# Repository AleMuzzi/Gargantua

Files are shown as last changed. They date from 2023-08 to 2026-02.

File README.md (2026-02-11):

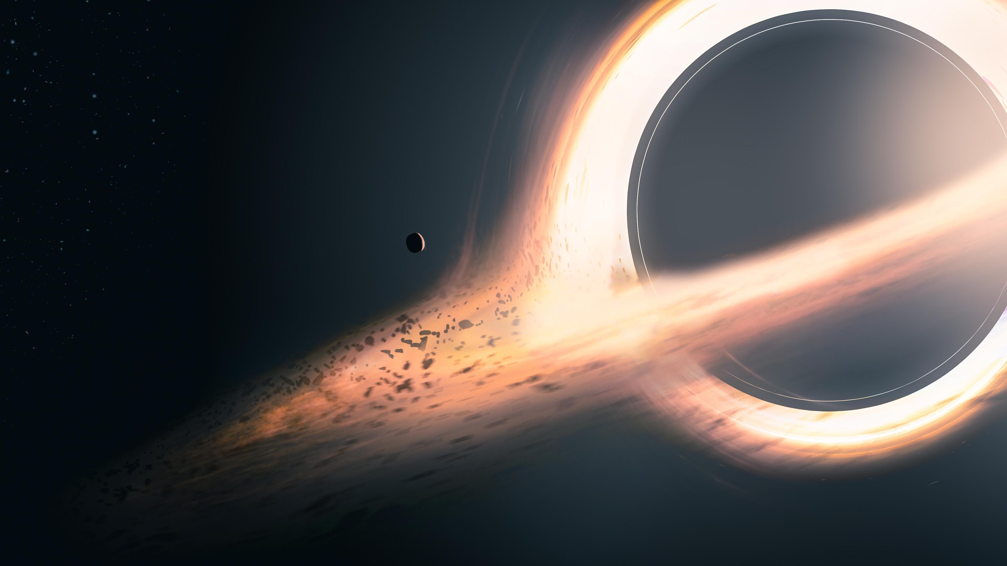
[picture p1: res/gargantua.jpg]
Gargantua Black Hole

# Gargantua - Large Format 3D Printer

With the prominence of the famous supermassive black hole, this is Gargantua!

Gargantua has a giant **430x420x770mm build volume** with double extruder and double independent Z axis to improve stability. Running **Klipper**, it enables for remote control from any device.

<p align="center">
  BTT Manta M8P
</p>

### Technical Specifications
```
Build Volume:           400x400x768 mm                   
Dimesions:                                        Extruders number:              2                   
    printer:            620x625x1145mm            Max extruders temperature:  300°      
    with case:         1020x890x1350mm            Max bed temperature:        110°         
    + dehumidifier:    1020x890x1790mm            Enclosure:                    Sì                          
Precision:                      0.1 mm            OS:                      Klipper                              
Max speed:                    300 mm/s            Power:               2x 24V 500W               
```
---

### Hardware

Choosing the firmware was the first major decision, as it influenced all subsequent hardware choices.
**Klipper** emerged as the winner due to its flexibility and ability to leverage 32-bit hardware for precise movement and temperature control.
I already had experience with Marlin, but I wanted to explore new possibilities and Klipper seemed like the right choice for this project.

<table align="right">
  <tr>
    <td align="center">
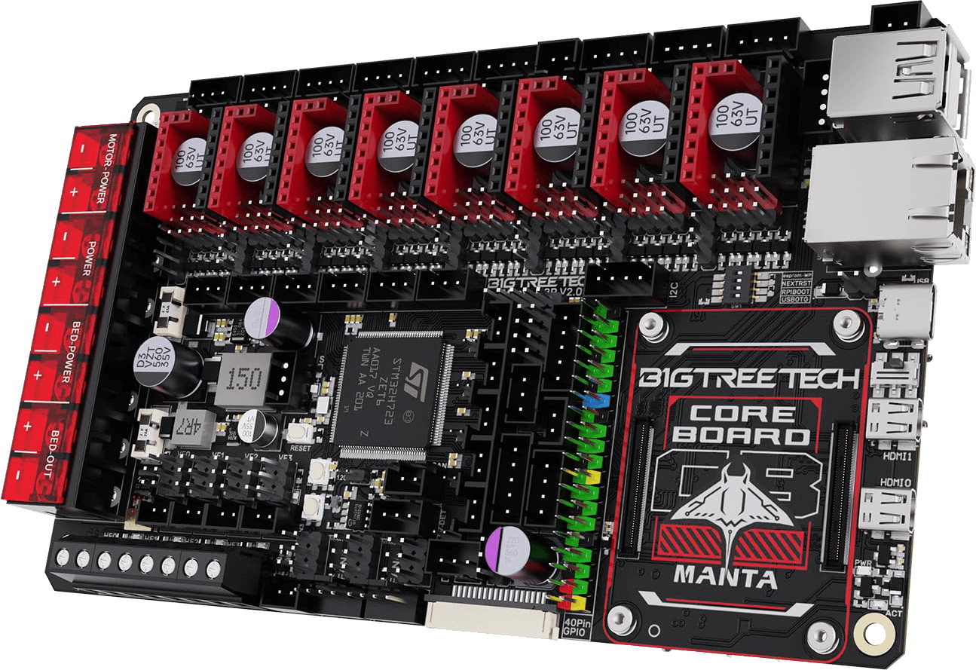
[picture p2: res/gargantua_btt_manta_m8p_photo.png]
BTT Manta M8P
      <br/>
      <sub><i>BTT Manta M8P</i></sub>
    </td>
  </tr>
</table>

For the controller I chose the **BTT Manta M8P** board, a 32-bit control board based on the STM32G0B1VET6, a 32-bit 64MHz ARM Cortex-M0+, which offers a wide range of features and good compatibility with various open source firmware.
It is paired with the **BTT CB1** computing module (essentially a twin to the Raspberry Pi CM4), which runs Klipper and manages the **Mainsail**[<math display="inline"><sup>↗</sup></math>](https://github.com/mainsail-crew/mainsail) user interface.

The next step was selecting the stepper motors. To reuse as many components as possible from my Ender 3 Pro, I decided to keep the same **NEMA 17** motors, which have proven reliable and suitable for the needs of this project, pairing them with a dual-axis **CR 42-60** motor for the Y-axis, drawing inspiration from the Creality CR-6 Max setup.

Also from the Creality CR-6 Max I took the heated bed, which offers a large printing surface of **400x400mm** and uniform heat distribution, and the idea of adding a couple of diagonal tie rods to improve the stability of the structure.

The motors are driven by **TMC2209** drivers, known for their silent operation and advanced microstepping.

<table align="right">
  <tr>
    <td align="center">
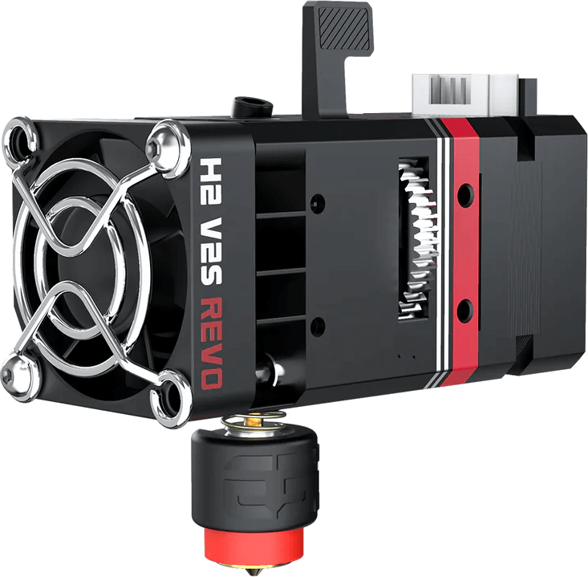
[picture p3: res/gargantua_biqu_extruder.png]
Biqu H2 V2S REVO
      <br/>
      <sub><i>Biqu H2 V2S REVO</i></sub>
    </td>
  </tr>
</table>

Because of the high power draw of the massive bed and dual hotends, I calculated the following power requirements:

The total power required by the main components of the printer is as follows:
- **Heated Bed:** 420W @ 24V
- **2x Biqu H2 V2S REVO Hotends (up to 300°):** 40W each
- **Filament Drying System (ongoing project):** 200W
- **Other components**: motors, fans, electronics
- **Safety margin**

So, I opted for **two 24V 500W power supplies**—one dedicated solely to the bed and the other for all other components. The bed is controlled via a **Solid State Relay (SSR)** for safety and reliability.

Finally, I upgraded the bed leveling sensor from a standard probe to a **Beacon H**[<math display="inline"><sup>↗</sup></math>](https://beacon3d.com/), which uses eddy current displacement to measure distance to accurately measure the distance between the sensor and the print bed, offering much more accurate, reliable and faster calibration, especially on larger surfaces. This allowed the bed mesh to leap from a 5x5 grid to a highly accurate 30x30 matrix without needing interpolation.

<p align="center">
  <video src="https://github.com/user-attachments/assets/059d04e4-c965-48ba-bb5d-aec4066f602b" width="40%" controls loop muted autoplay playsinline/>
</p>
<p align="center">
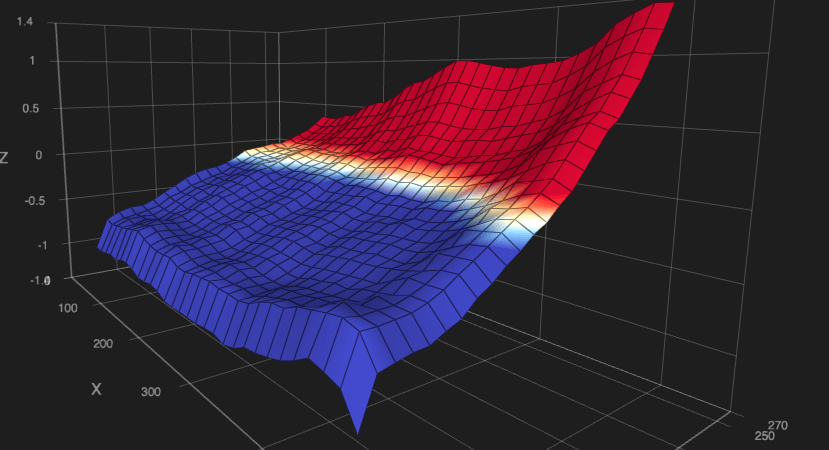
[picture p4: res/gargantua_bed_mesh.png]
Gargantua bed mesh
  
</p>

<p align="center">
  <sub><i>The plate seems very tilted, but if you look carefully at the Z-axis, on 40cm of length there is only 2mm of maximum difference</i></sub>
</p>

### Design and Development

The printer design was done using **Fusion 360**, which allowed me to precisely design each component, simulate axis movement, and verify the integration of all hardware components. I created detailed 3D models for every part of the printer, including motor mounts, heated dish brackets, electronics mounts, and cooling components.
The development process was iterative, with frequent testing and design changes. Designing everything in CAD allowed me to identify and resolve potential compatibility and space issues before proceeding to the assembly phase, saving time and resources.
The project was initially manageable in size, but over time it was necessary to break it down into parts and combine them into a single design for when an overall view is needed. This modularity allowed for more agile development of the various components.

<p align="center">
  Gargantua printer structure<br/>
  <sub><i>Gargantua's structure</i></sub>
</p>

#### From Bowden to Direct Drive

The Creality Ender 3 Pro uses a "bowden" extrusion system, in which the extruder is separated from the hotend and the filament is pushed through a tube to the hotend.
This approach has some advantages, such as reducing weight on the X-axis, but can present problems of reactivity and precision in extrusion, especially with flexible materials. I had already had difficulty with this system when trying to print TPU, which tended to bend inside the bowden tube, so I decided to switch to a "direct drive" system, where the extruder is mounted directly on the hotend. This change significantly improved the precision and responsiveness of the extrusion, allowing me to print a wider range of materials with greater reliability.
In designing this printer, flexibility took priority over performance; if I were to start over with a CoreXY system, I would probably opt for a bowden extrusion system, to reduce the weight on the X-axis and improve printing speed, at the cost of not being able to print flexible materials.

#### Dual Extruder

The idea of being able to print with two extruders has always fascinated me: in addition to allowing printing in 2 colors, it allows you to experiment with different materials, such as prints in which a flexible and a non-flexible material are interleaved, or to use soluble media such as PVA.
I then decided to implement it from the beginning, designing a support head for two Biqu H2 V2S REVO hotends.

<p align="center">
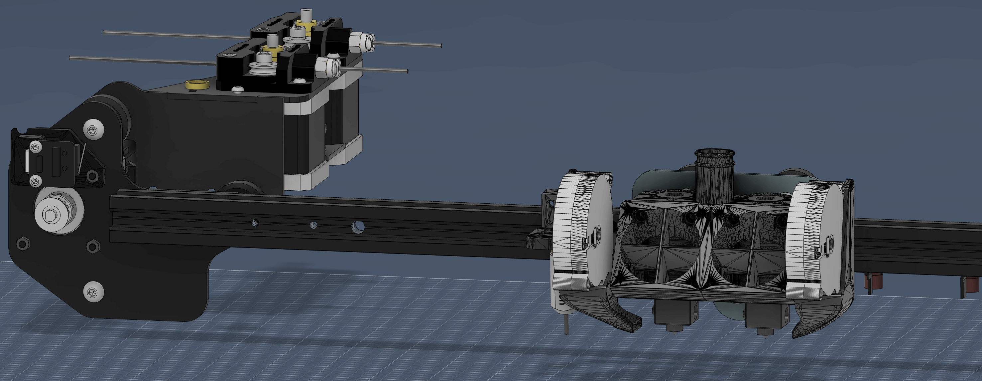
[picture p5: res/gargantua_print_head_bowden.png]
Gargantua bowden print head
  <br/>
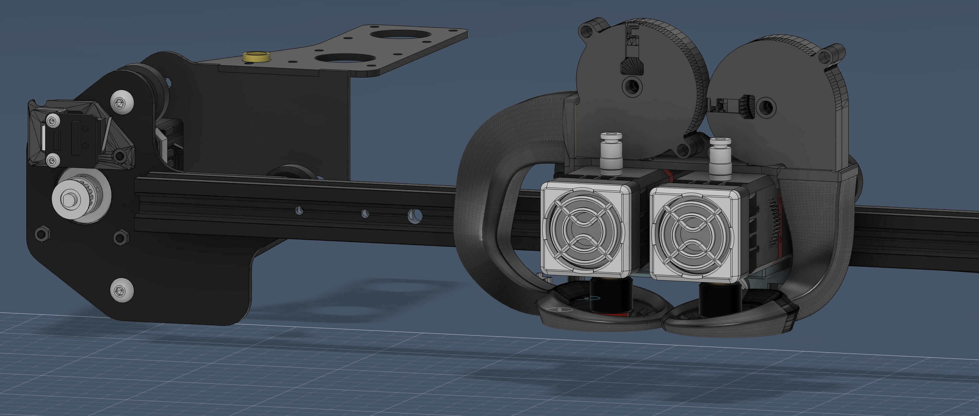
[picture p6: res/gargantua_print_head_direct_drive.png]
Gargantua direct drive print head
  <br/>
  <sub><i>(above) Bowden extruder, (below) Direct drive extruder</i></sub>
</p>

In the images above you can see the difference between the print head with bowden extruders and the one with direct drive extruders.
In the first, you can glimpse the extruders and the aeration channels to cool them (hidden fans to show the details), and in the distance on the left, the extruder motors.
In the second, however, you can see the two extruder motors mounted directly on the hotends on the print head. The metal profile where the motors for the bowden system were housed was left mounted to have an anchor for the cables going to the head.

In addition to the extruders, it can be noted that the aeration channels of the workpiece, fed by two radial fans, have also been improved, to allow for more homogeneous cooling.

#### Enclosure
To improve print quality, reduce noise during printing, and issues related to warping parts when printing materials like ABS, I decided to build a printer enclosure, a structure that completely encloses the printer, maintaining a stable internal temperature and reducing the influence of external air currents.
I already had experience building enclosures, for my Ender 3 Pro I had built what on the internet is called "IKEA Lack Enclosure"[<math display="inline"><sup>↗</sup></math>](https://www.google.com/search?q=ikea+lack+enclosure): using two overlapping IKEA Lack coffee tables, plexiglass panels for the side walls and doors, and 3D printing the various connectors.
As a first enclosure it might have been fine, but the IKEA Lack coffee table did not provide the necessary stability, and in any case it would not have been a solution applicable to a large printer like Gargantua.

For Gargantua, I drew a hollow aluminum square-section profile structure, with two ports, so that I had both front and side access to the printer.

<p align="center">
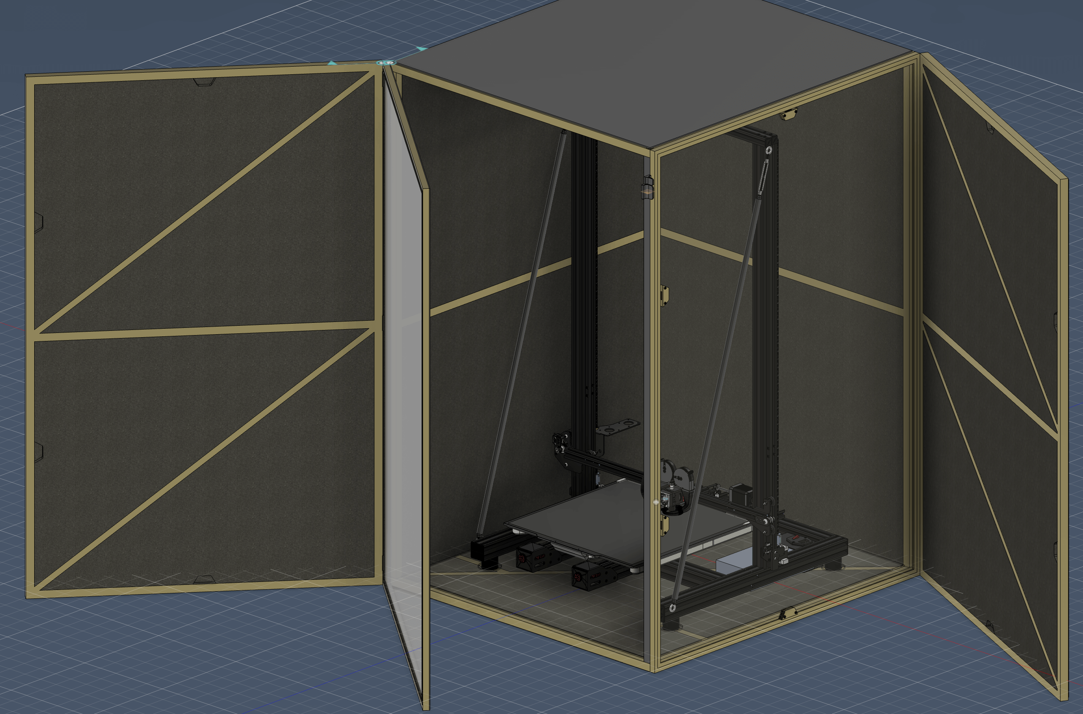
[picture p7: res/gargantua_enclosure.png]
Gargantua enclosure
  <br/>
  <sub><i>Gargantua inside its enclosure</i></sub>
</p>

The walls and doors were then padded with insulation panels and covered with hard plastic panels.
To allow me to inspect the printing in progress without having to open the doors, I designed the doors with a double hinge, so that the outer part can be opened independently of the inner part, consisting of an aluminum frame with a transparent plexiglass panel.
Inside, the printer is attached to the enclosure through 4 rubber dampers, to reduce vibrations transmitted to the structure, which is also equipped with rubber dampers such as feet.

> ℹ️ The enclosure is necessarily non-square in base to minimize the size while leaving room for the plate to slide along the Y-axis.

A strip led system was installed on the ceiling of the enclosure, to illuminate the interior during printing and facilitate visual inspection of the printing process.

<p align="center">
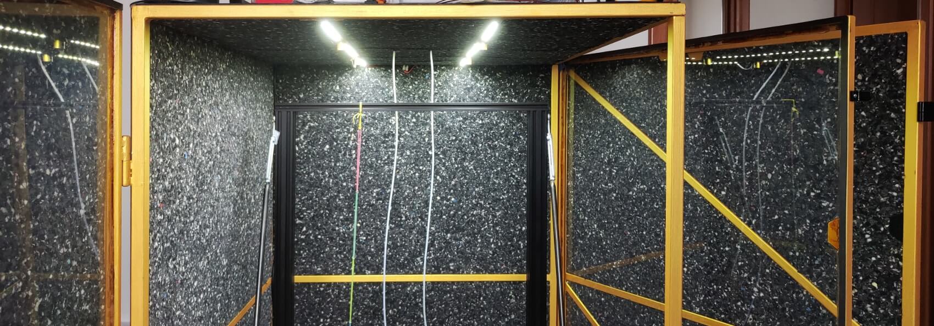
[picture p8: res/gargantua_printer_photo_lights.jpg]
Gargantua lights
  
</p>

### Filament Dehumidifier

A crucial and often underestimated part of 3D printing is the management of filaments, which are hygroscopic and tend to absorb moisture from the environment, resulting in a degradation of print quality. A wet filament expands and can cause under-extrusion problems, or even extruder blockages.
To address this issue, I decided to integrate a filament drying system directly above the enclosure, designing a dedicated compartment that houses 10 filaments, with a heating and ventilation system to keep the filaments dry and ready for printing.
This system is powered together with the printer, and is connected directly to the extruders, so that the dried filaments do not come into contact with external moisture on the way to the hotends.

<p align="center">
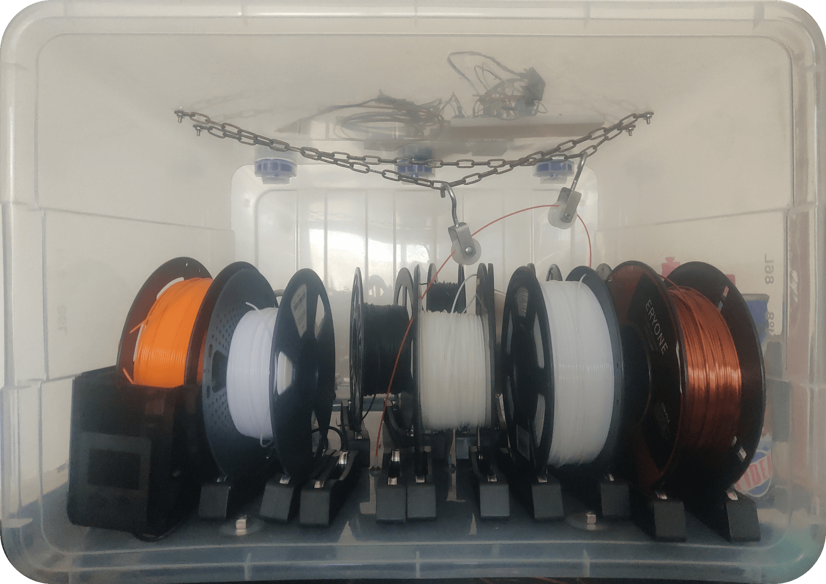
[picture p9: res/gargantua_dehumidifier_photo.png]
Gargantua dehumidifier
  <br/>
  <sub><i>Filament dehumidifier</i></sub>
</p>

In the photo above, you can see the dehumidifier, with several filaments, and above it, you can see the heating circuit, still in the prototyping phase. In the center, a pulley system guides the filaments toward the extruders; at the bottom center, you can see the tube that carries the filaments out of the dehumidifier, toward the extruders.

The system is still in development; the circuit is ready and tested, but some modifications to the 3D design are still needed to better integrate the components and improve airflow.

### Fume Management

Printing with materials such as ABS can generate potentially harmful fumes, as well as an unpleasant odor. To improve safety and comfort during printing, I decided to integrate a smoke extraction system directly into the enclosure.
Since I didn't have access to an external exhaust, I opted for an air filtration system based on activated carbon and HEPA filters, which capture particles and neutralize odors before reintroducing air into the environment.
The filter in question is the **AlveoOne R of Alveo3D**[<math display="inline"><sup>↗</sup></math>](https://www.alveo3d.com/en/product/alveoone-r-assembled/), designed specifically for 3D printing, it filters the air present in the enclosed case.
Gargantua's firmware is configured to automatically activate the fume extraction system when fume-generating materials are printed, and to continue filtering the air for a certain period after printing has finished.

### The Name: Gargantua
<p align="center">
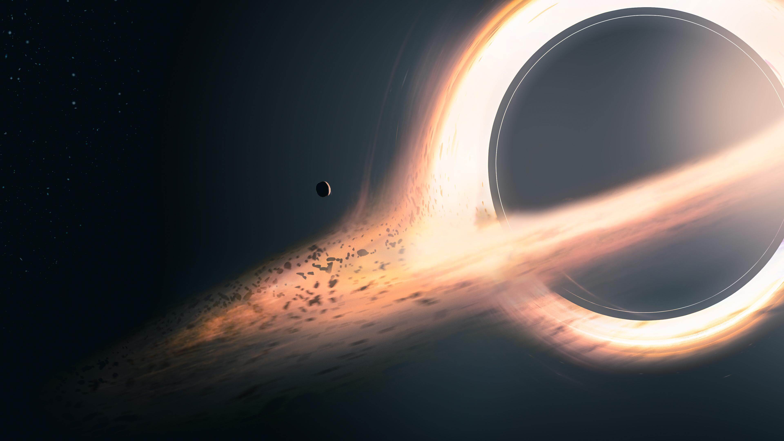
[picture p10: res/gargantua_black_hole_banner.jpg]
Gargantua black hole banner
  <br/>
  <sub><i>Gargantua - Interstellar's supermassive black hole</i></sub>
</p>

The name Gargantua was chosen in honor of the super-massive black hole depicted in Christopher Nolan's film Interstellar.
Gargantua was at the center of the film, depicted as a rotating black hole with a bright accretion disk and gravitational distortions that alter its appearance.

The name was chosen to symbolize the size and power of the printer, which, with its large print volume of **400x400x768mm** and its capabilities, represents a benchmark in my journey of learning and experimenting in the world of 3D printing.

### Lessons Learned

It would be nice to be able to say that everything went smoothly, but unfortunately it did not. This project presented numerous challenges and obstacles along the way, many of which stemmed from my inexperience in designing a 3D printer from scratch.
The main ones were 2: underestimating the temperatures inside the house and the erosion of the hotend nozzles.

The previous table-based enclosure IKEA Lack was not insulated, and the printer inside dissipated the heat generated during printing, maintaining a relatively low internal temperature.
After completing assembly and starting printing, I was pleased to see that the internal temperature of the case rose rapidly, reaching peaks of over 50°C and then remaining stable, a sign that the enclosure was doing its job.
However, this heat caused overheating problems for the electronics and power supplies, leading to malfunctions and printing interruptions.
To solve this problem, I had to drill a small hole in the back of the enclosure to move all the electronics outside, allowing for better heat dissipation.

<p align="center">
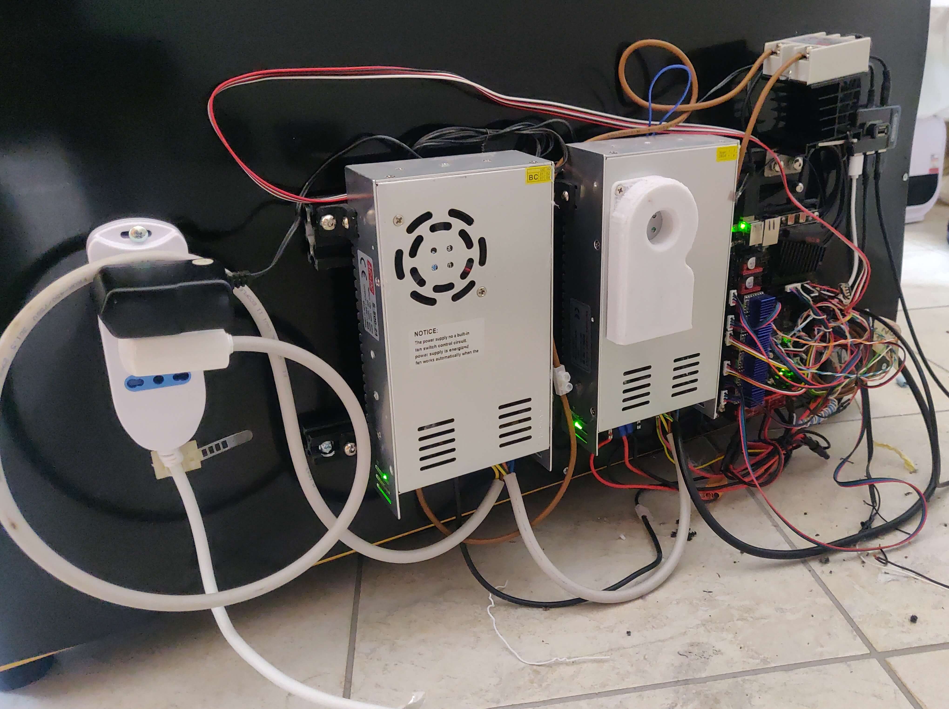
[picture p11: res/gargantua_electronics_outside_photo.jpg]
  
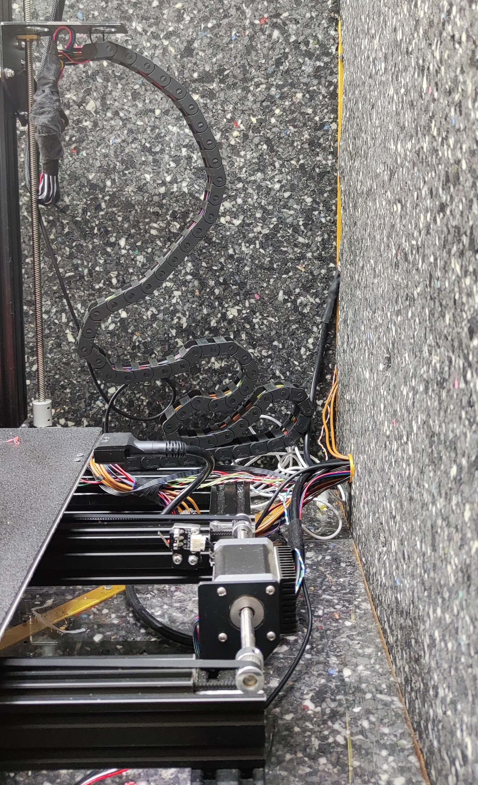
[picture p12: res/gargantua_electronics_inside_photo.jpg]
  
  <br/>
  <sub><i>(left) Power supplies and electronics moved outside. (right) Cables inside.</i></sub>
</p>

The second problem was the erosion of the hotend nozzles. When I made the double extruder printhead, I tried to get as much precision as possible, to make sure that the height of the two hotends was perfectly aligned.
However, the dual extruder operated for a short time: erosions from printing and nozzles that left the factory slightly higher than others made it impossible to maintain precise alignment between the two hotends. Unfortunately, the accuracy required here is quite high, ~0.1mm, and even a small difference in height between the two hotends can cause printing problems.
For this reason, I am currently printing with a single extruder, but I am working on a new print head and am evaluating several options:
- mobile extruder system, in which the extruders move up and down and are individually calibrated
- IDEX (Independent Dual Extrusion) system, in which the two extruders are completely independent and can move autonomously, completely eliminating the alignment problem.

Or maybe both!

### Results and Future Developments
This was certainly the most ambitious and complex project I have ever carried out, and despite the challenges I encountered, I am extremely satisfied with the final result.
Gargantua is a large format, powerful and versatile 3D printer, which has allowed me to explore new possibilities in 3D printing and improve my skills in design and electronics.
I can't say it's over, because this is an ever-evolving project, with new features and improvements in development, but I'm proud of what I've accomplished so far and can't wait to see where this project takes me in the future.

<p align="center">
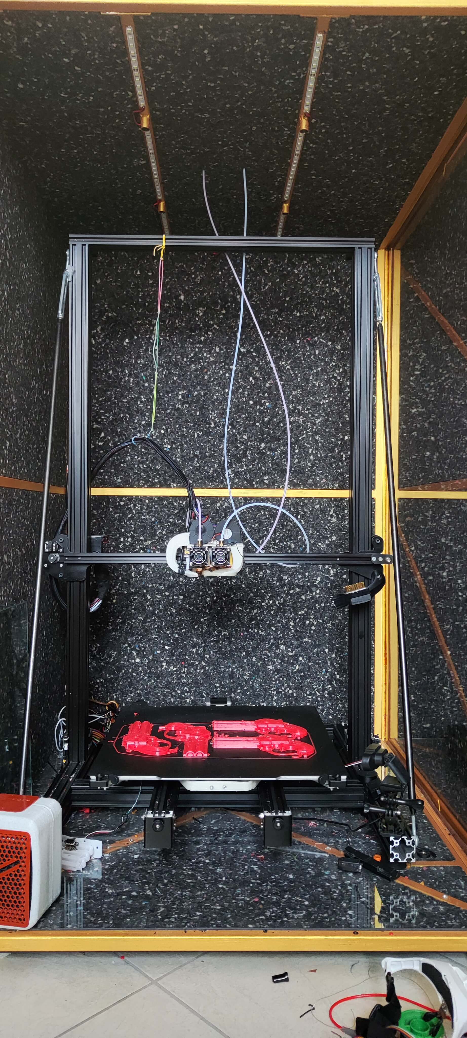
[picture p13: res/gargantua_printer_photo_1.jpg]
  
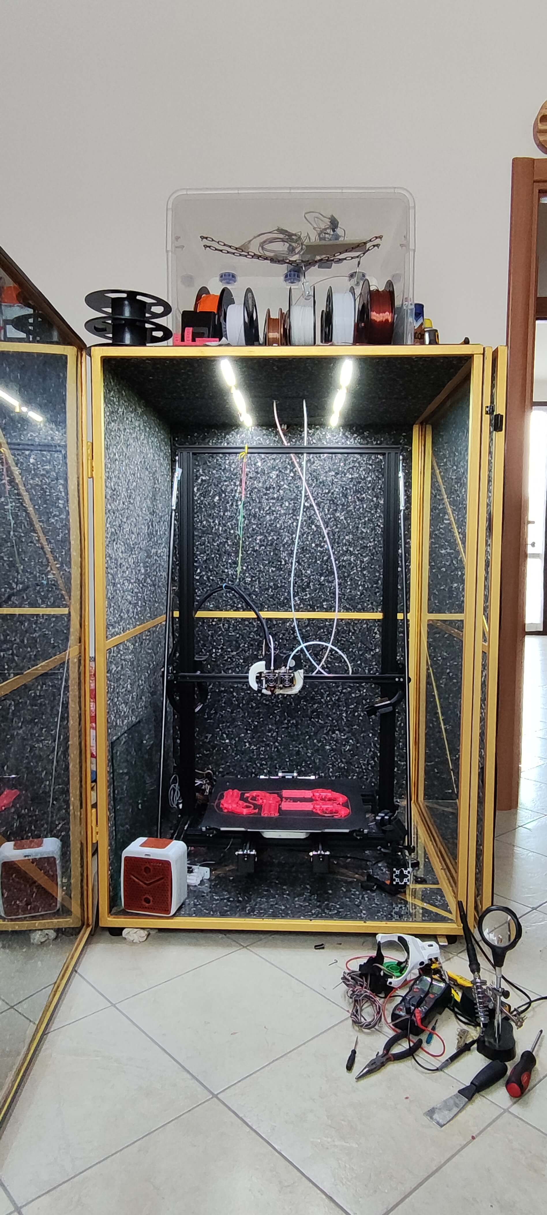
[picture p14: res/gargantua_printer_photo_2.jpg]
  
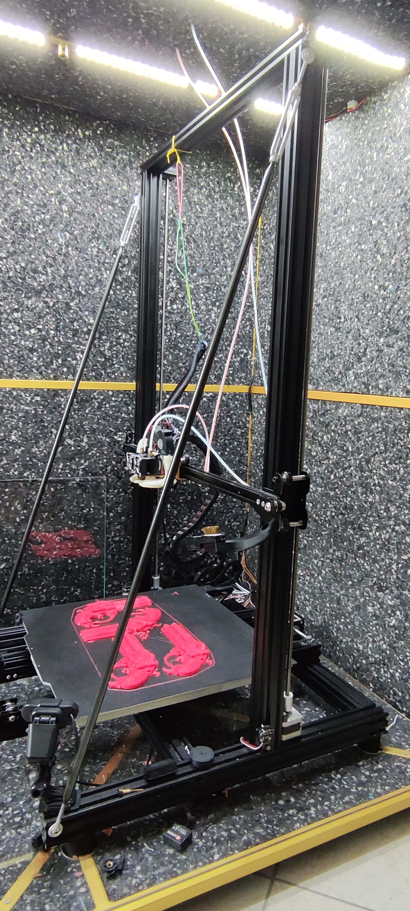
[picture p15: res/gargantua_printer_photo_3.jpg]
  
</p>

## Technologies and tools
* **Firmware:** Klipper
* **Hardware:** BTT Manta M8P, BTT CB1, NEMA 17, CR 42-60, TMC2209, SSR
* **User Interface:** Mainsail
* **Slicers:** Cura, PrusaSlicer
* **Design:** Fusion 360

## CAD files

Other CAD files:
Design/X, Z Axis & frame.3mf
Design/X Axis Dual Extruder.3mf
Design/Z Axis & frame.3mf
Design/Gargantua.3mf
Design/Y Axis.3mf
Design/Gargantua.f3z
Design/X Axis Dual Extruder.f3d
Design/X, Z Axis & frame.f3z
Design/Y Axis.f3d
Design/Z Axis & frame.f3d

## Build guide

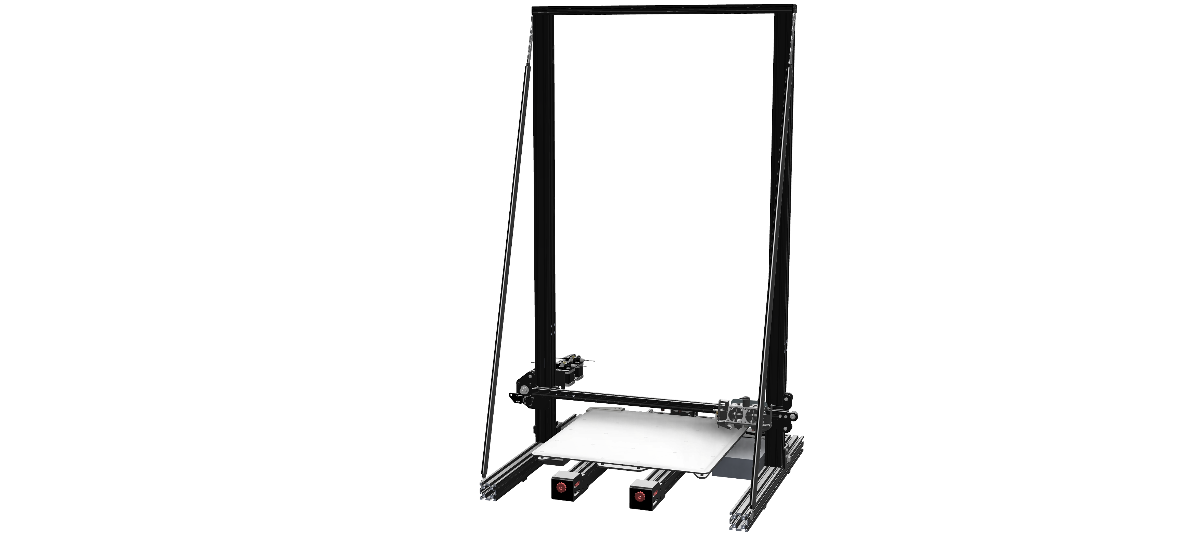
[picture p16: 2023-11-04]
res/Gargantua_printer.png

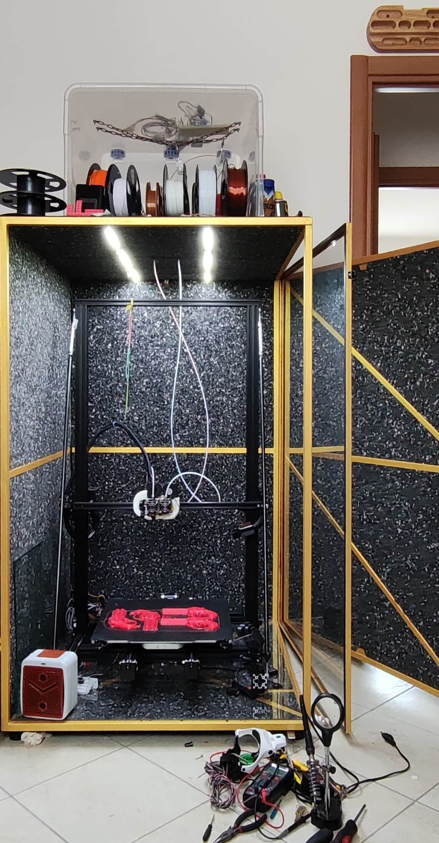
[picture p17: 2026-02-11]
res/gargantua_printer_photo_5.jpg

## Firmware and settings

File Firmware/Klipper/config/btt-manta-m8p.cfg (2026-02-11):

# This file contains common pin mappings for the BIGTREETECH Manta M8P
# To use this config, the firmware should be compiled for the
# STM32G0B1 with a "8KiB bootloader" and USB communication.

# See docs/Config_Reference.md for a description of parameters.

[stepper_x]
step_pin: PE2
dir_pin: !PB4
enable_pin: !PC11
microsteps: 256
rotation_distance: 40
endstop_pin: ^PF3
position_endstop: 0
position_max: 545
homing_speed: 50

[tmc2209 stepper_x]
uart_pin: PC10
diag_pin: PF3
run_current: 0.714
interpolate: False
;hold_current: 0.42  ; commented due to https://www.klipper3d.org/TMC_Drivers.html#prefer-to-not-specify-a-hold_current
stealthchop_threshold: 999999

[stepper_y]
step_pin: PF12
dir_pin: PF11
enable_pin: !PB3
microsteps: 256
rotation_distance: 40
endstop_pin: ^PF4
position_endstop: 0
position_max: 270
homing_speed: 50

[tmc2209 stepper_y]
uart_pin: PF13
diag_pin: PF4
run_current: 0.9
interpolate: False
;run_current: 1.1
;hold_current: 0.7
stealthchop_threshold: 999999

[stepper_z]
step_pin: PD7
dir_pin: PD6
enable_pin: !PF10
microsteps: 256
rotation_distance: 8
endstop_pin: ^PF5
position_endstop: 0
position_max: 760
position_min: -3
homing_speed: 20
second_homing_speed: 10
homing_retract_dist: 3


[tmc2209 stepper_z]
uart_pin: PF9
diag_pin: PF5
run_current: 0.65
interpolate: False
;hold_current: 0.42
stealthchop_threshold: 999999

[stepper_z1]
step_pin: PD3
dir_pin: PD2
enable_pin: !PD5
microsteps: 256
rotation_distance: 8
endstop_pin: ^!PC0

[tmc2209 stepper_z1]
uart_pin: PD4
diag_pin: PC0
run_current: 0.65
interpolate: False
;hold_current: 0.42
stealthchop_threshold: 999999


# Motor4
# The M8P only has 4 heater outputs which leaves an extra stepper
# This can be used for a second Z stepper, dual_carriage, extruder co-stepper,
# or other accesory such as an MMU
#[stepper_z2]
#step_pin: PD3
#dir_pin: PD2
#enable_pin: PD5
#endstop_pin: PC0
#...

[thermistor Trianglelab-NTC100K-B3950]
temperature1: 25
resistance1: 103180
temperature2: 150
resistance2: 1366.2
temperature3: 250
resistance3: 168.6


[extruder]
step_pin: PC9
dir_pin: !PC8
enable_pin: !PD1
microsteps: 256
rotation_distance: 3.433
nozzle_diameter: 1.4
filament_diameter: 1.75
heater_pin: PE3 # HE0
sensor_pin: PA1 # TH0
sensor_type: Trianglelab-NTC100K-B3950
control: pid
pid_Kp:11.118
pid_Ki:0.380
pid_Kd:81.303
min_temp: 0
max_temp: 300
min_extrude_temp: 0
max_extrude_only_distance: 100

[tmc2209 extruder]
uart_pin: PD0
run_current: 0.75
interpolate: False
stealthchop_threshold: 999999

[verify_heater extruder]
max_error: 1000

# Script to change back to the main extruder
[gcode_macro T0]
gcode:
    #SET_SERVO SERVO=extruder_servo angle=100    # Lift secondary extruder
    #SET_GCODE_OFFSET Z=0 MOVE=1                 # Adjust z-height
    #SET_GCODE_OFFSET X=0                        # Clear X offset
    ACTIVATE_EXTRUDER EXTRUDER=extruder



#[extruder1]
#step_pin: PA10
#dir_pin: !PA14
#enable_pin: !PA15
#microsteps: 256
#rotation_distance: 3.433
#nozzle_diameter: 1.4
#filament_diameter: 1.75
#heater_pin: PB5 # HE1
#sensor_pin: PA2 # TH1
#sensor_type: Trianglelab-NTC100K-B3950
#control: pid
#pid_Kp:11.118
#pid_Ki:0.380
#pid_Kd:81.303
#min_temp: 0
#max_temp: 300
#min_extrude_temp: 0
#max_extrude_only_distance: 100

#[tmc2209 extruder1]
#uart_pin: PF8
#run_current: 0.75
#interpolate: False
#stealthchop_threshold: 999999

#[verify_heater extruder1]
#max_error: 1000

# Script to activate second extruder
[gcode_macro T1]
gcode:
    #SET_GCODE_OFFSET Z=0.100 MOVE=1             # Adjust z-height
    #SET_SERVO SERVO=extruder_servo angle=100    # Position second extruder
    #SET_GCODE_OFFSET X=5                        # Account for different X offset
    ACTIVATE_EXTRUDER EXTRUDER=extruder1


[verify_heater heater_bed]
max_error: 40000
#   The maximum "cumulative temperature error" before raising an
#   error. Smaller values result in stricter checking and larger
#   values allow for more time before an error is reported.
#   Specifically, the temperature is inspected once a second and if it
#   is close to the target temperature then an internal "error
#   counter" is reset; otherwise, if the temperature is below the
#   target range then the counter is increased by the amount the
#   reported temperature differs from that range. Should the counter
#   exceed this "max_error" then an error is raised. The default is
#   120.


#[filament_switch_sensor material_0]
#switch_pin: PC1


[heater_bed]
heater_pin: PB7
sensor_pin: PA0 # TB
sensor_type: Trianglelab-NTC100K-B3950
control: pid
pid_Kp: 100.492
pid_Ki: 1.5
pid_Kd: 1477.762
min_temp: 0
max_temp: 115

[fan]
pin: PC12

[fan_generic alveo_fan]
pin: PB8


[heater_fan fan1]
pin: PE6
heater: extruder
heater_temp: 50.0

#[heater_fan fan2]
#pin: PE0
#heater: extruder1
#heater_temp: 50.0

[safe_z_home]
home_xy_position: 0, 4
z_hop: 11.0 # with alluminium sheet
#z_hop: 8.0

[force_move]
enable_force_move: True

[filament_switch_sensor filament_sensor]
pause_on_runout: True
switch_pin: ^PC5

[gcode_button emergency_stop]
# The pin your button is connected to. The '^' enables the
# internal pull-up resistor, which is highly recommended for reliability.
pin: ^!PC2 

press_gcode: {action_emergency_stop("Emergency stop button pressed!")}
release_gcode: FIRMWARE_RESTART

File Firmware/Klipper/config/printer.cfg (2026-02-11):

[mcu]
serial: /dev/serial/by-id/usb-Klipper_stm32g0b1xx_3E0015000D504B4633373520-if00
restart_method: command
#timeout: 0.050

#[mcu cb1]
#serial: /tmp/klipper_host_mcu

#[gcode_shell_command usb_reset]
#command: >
#  echo 0 > /sys/bus/usb/devices/usb1/authorized;
#  sleep 1;
#  echo 1 > /sys/bus/usb/devices/usb1/authorized
#timeout: 10.0

#[gcode_macro FIRMWARE_RESTART]
#rename_existing: FIRMWARE_RESTART_BASE
#gcode:
#  RUN_SHELL_COMMAND CMD=usb_reset
#  G4 P2000  # Wait 2 seconds
#  FIRMWARE_RESTART_BASE

[printer]
kinematics: cartesian
max_velocity: 500
max_accel: 1500
max_z_velocity: 5
max_z_accel: 200

[board_pins]
aliases:
    # EXP1 header
    EXP1_1=PE9, EXP1_2=PE10,
    EXP1_3=PE11, EXP1_4=PE12,
    EXP1_5=PE13, EXP1_6=PE14,    # Slot in the socket on this side
    EXP1_7=PE15, EXP1_8=PB10,
    EXP1_9=<GND>, EXP1_10=<5V>,

    # EXP2 header
    EXP2_1=PB14, EXP2_2=PB13,
    EXP2_3=PF7, EXP2_4=PB12,
    EXP2_5=PE7, EXP2_6=PB11,      # Slot in the socket on this side
    EXP2_7=PE8, EXP2_8=<RST>,
    EXP2_9=<GND>, EXP2_10=PC5

[include mainsail.cfg]

[include btt-manta-m8p.cfg]

[exclude_object]

[include add-ons/*.cfg]

#*# <---------------------- SAVE_CONFIG ---------------------->
#*# DO NOT EDIT THIS BLOCK OR BELOW. The contents are auto-generated.
#*#
#*# [beacon model default]
#*# model_coef = 1.5463438349930179,
#*# 	  1.887375763214759,
#*# 	  0.8292515262666169,
#*# 	  0.30329923252568564,
#*# 	  0.11500697992094581,
#*# 	  0.5155505314263574,
#*# 	  0.0612498363974414,
#*# 	  -0.7176363511299747,
#*# 	  0.04796985317455004,
#*# 	  0.413319200037929
#*# model_domain = 1.8502994917827975e-07,1.934825183309776e-07
#*# model_range = 0.200000,5.000000
#*# model_temp = 58.040133
#*# model_offset = 0.00000
#*#
#*# [bed_mesh default]
#*# version = 1
#*# points =
#*# 	-0.828522, -0.839875, -0.826041, -0.807475, -0.828911, -0.791586, -0.782397, -0.809593, -0.848442, -0.845897, -0.831217, -0.847264, -0.889044, -0.900220, -0.890778, -0.891836, -0.891622, -0.878203, -0.872576, -0.900559, -0.876047, -0.820413, -0.805771, -0.781362, -0.749018, -0.696098, -0.627604, -0.652295, -0.686178, -0.873363
#*# 	-0.557265, -0.587859, -0.572709, -0.563149, -0.548987, -0.528773, -0.510868, -0.553365, -0.584667, -0.600756, -0.599366, -0.591579, -0.635019, -0.639850, -0.618574, -0.613632, -0.599649, -0.616230, -0.616284, -0.622894, -0.601324, -0.548075, -0.511798, -0.504277, -0.453094, -0.427876, -0.401512, -0.382218, -0.412841, -0.585291
#*# 	-0.498849, -0.540167, -0.525076, -0.550432, -0.519664, -0.506492, -0.479262, -0.504313, -0.544992, -0.562259, -0.540912, -0.554796, -0.593616, -0.613509, -0.600165, -0.592547, -0.609220, -0.608718, -0.601667, -0.618272, -0.575705, -0.550072, -0.517663, -0.515264, -0.495181, -0.442096, -0.364475, -0.404289, -0.415809, -0.561755
#*# 	-0.465207, -0.517441, -0.510845, -0.514365, -0.496883, -0.465776, -0.477483, -0.513574, -0.533876, -0.555061, -0.554767, -0.555300, -0.580347, -0.589114, -0.579782, -0.550870, -0.560677, -0.586443, -0.603894, -0.602391, -0.545997, -0.526320, -0.517489, -0.493207, -0.479201, -0.459111, -0.412090, -0.398500, -0.407000, -0.540462
#*# 	-0.462645, -0.490631, -0.515081, -0.533835, -0.523394, -0.491240, -0.493931, -0.524878, -0.542658, -0.535343, -0.514256, -0.536768, -0.579890, -0.593306, -0.576073, -0.556758, -0.567865, -0.591152, -0.599450, -0.596708, -0.555728, -0.532435, -0.520686, -0.504360, -0.487273, -0.465094, -0.382757, -0.396752, -0.398658, -0.535741
#*# 	-0.417822, -0.458821, -0.469761, -0.483330, -0.465991, -0.461761, -0.487148, -0.499170, -0.509402, -0.508374, -0.505727, -0.520272, -0.555079, -0.557158, -0.535275, -0.526564, -0.518464, -0.532977, -0.560103, -0.563614, -0.522118, -0.508592, -0.482006, -0.484647, -0.444957, -0.426893, -0.403616, -0.365893, -0.365791, -0.484838
#*# 	-0.352764, -0.383742, -0.404384, -0.412683, -0.439968, -0.415623, -0.417402, -0.440340, -0.452337, -0.457384, -0.434048, -0.451144, -0.504233, -0.504801, -0.481886, -0.478613, -0.488099, -0.498853, -0.510683, -0.503232, -0.480966, -0.467768, -0.455491, -0.443386, -0.435384, -0.378499, -0.320910, -0.324557, -0.318563, -0.444338
#*# 	-0.293890, -0.346128, -0.347944, -0.347081, -0.374251, -0.349104, -0.372837, -0.404357, -0.417521, -0.434016, -0.417229, -0.433493, -0.462579, -0.455729, -0.440827, -0.423246, -0.420606, -0.439805, -0.457292, -0.431671, -0.416473, -0.398202, -0.392614, -0.380668, -0.360748, -0.337457, -0.303436, -0.261348, -0.251691, -0.352983
#*# 	-0.228363, -0.287184, -0.293467, -0.297508, -0.328823, -0.304030, -0.307329, -0.350374, -0.369660, -0.377712, -0.355770, -0.372506, -0.410187, -0.398805, -0.392670, -0.384125, -0.396874, -0.418944, -0.425727, -0.384686, -0.380884, -0.371036, -0.349003, -0.352905, -0.349887, -0.299130, -0.212661, -0.203137, -0.192904, -0.294776
#*# 	-0.180912, -0.254548, -0.266451, -0.256584, -0.240932, -0.255513, -0.278131, -0.310570, -0.317634, -0.345610, -0.336764, -0.354667, -0.384936, -0.372386, -0.369745, -0.346774, -0.339918, -0.365027, -0.373787, -0.334917, -0.326878, -0.314256, -0.298540, -0.305466, -0.292860, -0.254223, -0.196623, -0.145901, -0.129197, -0.211735
#*# 	-0.149279, -0.212590, -0.209982, -0.219751, -0.203383, -0.214699, -0.218908, -0.261714, -0.290436, -0.308391, -0.287229, -0.296449, -0.341006, -0.333993, -0.317029, -0.306951, -0.314255, -0.338118, -0.339906, -0.304672, -0.299511, -0.279446, -0.274683, -0.271440, -0.250223, -0.191833, -0.099365, -0.082879, -0.062390, -0.146614
#*# 	-0.135212, -0.189094, -0.196232, -0.172256, -0.155252, -0.146741, -0.181674, -0.229769, -0.235454, -0.262187, -0.253868, -0.255403, -0.308248, -0.302701, -0.285847, -0.265676, -0.250850, -0.279596, -0.280994, -0.250798, -0.244640, -0.204581, -0.225343, -0.207781, -0.184275, -0.143335, -0.084180, -0.023261, 0.002278, -0.063441
#*# 	-0.100104, -0.132025, -0.127127, -0.136377, -0.113935, -0.102826, -0.127768, -0.182127, -0.208131, -0.219842, -0.190845, -0.207215, -0.252630, -0.251638, -0.220568, -0.220203, -0.218842, -0.246898, -0.245081, -0.228347, -0.230867, -0.190266, -0.191086, -0.167085, -0.132692, -0.080877, 0.007445, 0.027150, 0.061022, -0.008101
#*# 	-0.050630, -0.093423, -0.091879, -0.081154, -0.062668, -0.082325, -0.113878, -0.142967, -0.136342, -0.143064, -0.133897, -0.147749, -0.186971, -0.179265, -0.173860, -0.168543, -0.147112, -0.176898, -0.168786, -0.160261, -0.163307, -0.122780, -0.121251, -0.101661, -0.061268, -0.012979, 0.044379, 0.102225, 0.137008, 0.081973
#*# 	0.015884, -0.035865, -0.035341, -0.043723, -0.048733, -0.036201, -0.075106, -0.097275, -0.089065, -0.094089, -0.079319, -0.082386, -0.104473, -0.129386, -0.103252, -0.107309, -0.110946, -0.131273, -0.110605, -0.122368, -0.120990, -0.083888, -0.071612, -0.026813, -0.003848, 0.060186, 0.153912, 0.182393, 0.216576, 0.152358
#*# 	0.034084, 0.002619, -0.018802, -0.032085, -0.024452, 0.010821, -0.012298, -0.043686, -0.043069, -0.053198, -0.036085, -0.045261, -0.079707, -0.071082, -0.057769, -0.046917, -0.014845, -0.031457, -0.014252, -0.026253, -0.009074, 0.017002, 0.031143, 0.071196, 0.107214, 0.155743, 0.223637, 0.288135, 0.329242, 0.271968
#*# 	0.046652, 0.003755, 0.005363, -0.000495, 0.008881, 0.042864, 0.021962, 0.000211, -0.013261, -0.013016, 0.018044, 0.016271, -0.008499, 0.013983, 0.035151, 0.049174, 0.064835, 0.046039, 0.050648, 0.034900, 0.055238, 0.071464, 0.104527, 0.130351, 0.173001, 0.237763, 0.350900, 0.400817, 0.442392, 0.389356
#*# 	0.071438, 0.035885, 0.034185, 0.025933, 0.040126, 0.078446, 0.065299, 0.051561, 0.052954, 0.048418, 0.078125, 0.085525, 0.060371, 0.087236, 0.107148, 0.136223, 0.168466, 0.160908, 0.144258, 0.128538, 0.160386, 0.176655, 0.199369, 0.230425, 0.265545, 0.325034, 0.425609, 0.502961, 0.556243, 0.512299
#*# 	0.070902, 0.022509, 0.044290, 0.035833, 0.050512, 0.077686, 0.075544, 0.059939, 0.065051, 0.076670, 0.115076, 0.122923, 0.112638, 0.162227, 0.163311, 0.214107, 0.197851, 0.197138, 0.187424, 0.175909, 0.199358, 0.226033, 0.240994, 0.283832, 0.315803, 0.388714, 0.513100, 0.574835, 0.626533, 0.580949
#*# 	0.108521, 0.074432, 0.075664, 0.072758, 0.085354, 0.126309, 0.130123, 0.125700, 0.145009, 0.155400, 0.199420, 0.220196, 0.208563, 0.252741, 0.264935, 0.318299, 0.323515, 0.306649, 0.293774, 0.312447, 0.331695, 0.331925, 0.366928, 0.401653, 0.432646, 0.495758, 0.606049, 0.686880, 0.749471, 0.707664
#*# 	0.158694, 0.112080, 0.124379, 0.123770, 0.141240, 0.174781, 0.188442, 0.188518, 0.208833, 0.230144, 0.282809, 0.314472, 0.319948, 0.363863, 0.394172, 0.433714, 0.438923, 0.416806, 0.400746, 0.402663, 0.410697, 0.445732, 0.457753, 0.497170, 0.534706, 0.607766, 0.738901, 0.806359, 0.866959, 0.830793
#*# 	0.198923, 0.173934, 0.185976, 0.187015, 0.207317, 0.253912, 0.276311, 0.291966, 0.322577, 0.345835, 0.405020, 0.450693, 0.457792, 0.503050, 0.547495, 0.593361, 0.613291, 0.592268, 0.569355, 0.560360, 0.564781, 0.607918, 0.622608, 0.643626, 0.693682, 0.759409, 0.883443, 0.965906, 1.020993, 1.000361
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

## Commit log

2024-05-02 Updated designs
    [Gargantua.3mf, Gargantua.f3z]
2026-02-11 Added designs & updated README.md
    [Gargantua.3mf, Gargantua.f3z, KAMP_Settings.cfg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]
